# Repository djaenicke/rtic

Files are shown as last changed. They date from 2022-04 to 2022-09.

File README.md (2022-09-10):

<p align="center">
  <h1 align="center">RTIC</h1>
</p>

### The Hardware
The Real Time Interface and Controller (RTIC) is a universal board for low-level robotics control and monitoring. The board can be ordered from [JLCPCB](https://jlcpcb.com/) using the [assembly](pcb/kicad/v2/assembly) and [gerber](pcb/kicad/v2/gerber) files.

#### Key Features
- 4 permanent magnet DC motor outputs
- 4 quadrature encoder inputs
- 6-axis IMU
- NRF24L01 socket for wireless communications
- USB (supports DFU via jumper)
- CAN breakout header

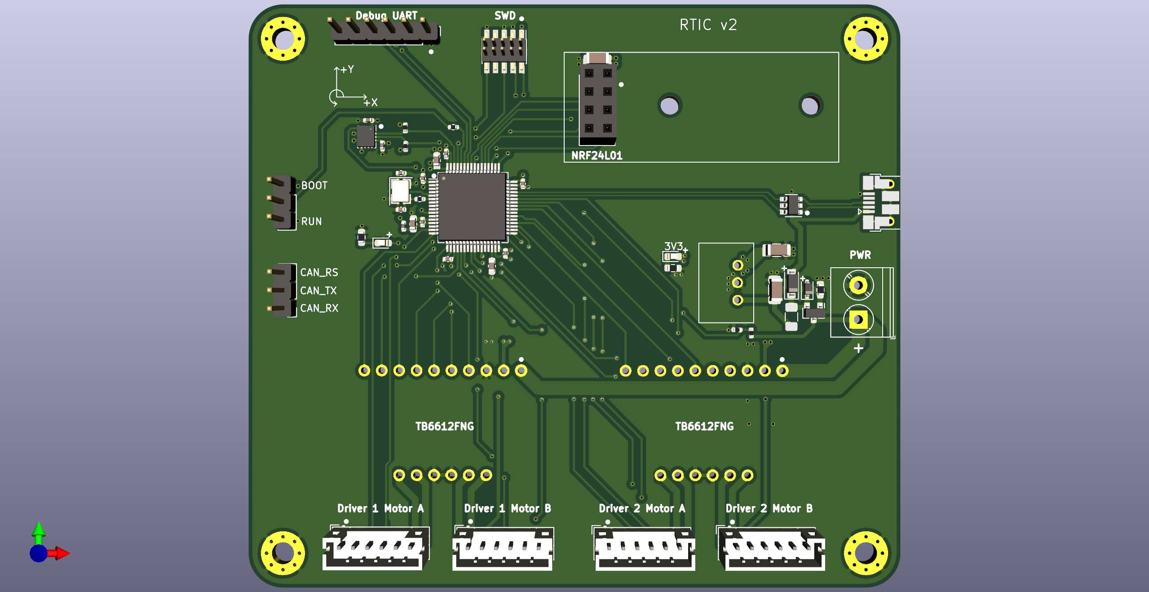
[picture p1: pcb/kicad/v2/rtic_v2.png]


A [compatible 4-wheeled mobile robot base](https://www.amazon.com/Moebius-Mecanum-Platform-Omni-direactional-Raspberry/dp/B083XS2SD7) can be purchased directly from Amazon. :robot:

### Tools Setup ✔️
At a minium you will need the ARM GNU GCC Toolchain, Make and CMake to compile the source and generate executable artifacts.
-   [ARM GNU GCC Toolchain - 10-2020-q4-major](https://developer.arm.com/tools-and-software/open-source-software/developer-tools/gnu-toolchain/gnu-rm/downloads) - Other versions can be used but the current source is actively developed and tested using the 10-2020-q4-major release
-   Make -  Make is shipped with Linux and should already be present on the developers system. If the developer is running Windows they can either use WSL to run a Linux instance or install Make on Windows via [MinGW](https://sourceforge.net/projects/mingw/)
-   [CMake](https://cmake.org/download/)

To flash and debug the target this project uses a couple of different tools. PyOCD, Segger JLink, or STLINK can be used as the programming/debugging medium, and a VScode extension called Cortex-Debug gives a user interface within VScode for stepping through the source, settings breakpoints and viewing registers/variables within the target.
-   [PyOCD](https://github.com/pyocd/pyOCD#installing)
-   [JLink](https://www.segger.com/downloads/jlink/)
-   [STLINK](https://github.com/stlink-org/stlink)
-   [VScode](https://code.visualstudio.com/)
-   [ARM Developer Extension Pack for VScode](https://marketplace.visualstudio.com/items?itemName=Glasslabs.arm-developer-toolkit)

As an alternative to the debuggging tools, dfu-util can be used to program the board using the built in DFU capability of the bootloader.
-   [dfu-util](https://manpages.ubuntu.com/manpages/xenial/man1/dfu-util.1.html)
    - Linux - ```sudo apt-get install dfu-util```

***NOTE: After installing your desired debug toolset, please ensure the chosen application is accessible from the command line (pyocd or JLinkExe)***

To format all source files, you will need to install Clang-Format.
-   [Clang-Format](https://clang.llvm.org/docs/ClangFormat.html)
    - Linux - ```sudo apt-get install clang-format```

### Compiling, Flashing & Testing ✨
After a fresh clone, the ```setup``` scripts can be used to initialize the project. Passing ```release``` as an argument will generate a release build. Otherwise a ```debug``` build is generated.
##### Windows
```console
setup.ps1
```
##### Linux
```console
./setup.sh
```

Once a project has been initialized, the following commands should be ran from the ```build/``` folder

To clean the working directory:
```console
make clean
```

To compile the source:
```console
make -j8
```

To erase the connected target with PyOCD or Segger JLink:
```console
make erase
```

To flash the connected target with PyOCD or Segger JLink:
```console
make flash
```

To flash the connected target via DFU:
```console
make dfu
```

To execute unit tests:
```console
make test
```

To format source files:
```console
make format
```

### Source Documentation Style 📃
Read more about the Source documentation style [here](./doc/DOCUMENTATION_STYLE.md)

### Develop Strategy 📖
Read more about the Git develop strategy used [here](./doc/DEVELOP_STRATEGY.md)

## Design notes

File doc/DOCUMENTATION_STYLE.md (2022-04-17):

### Documentation Style
All of the source files should be commented/documented using Doxygen style comments. This has two benefits: 1.) The code is well documented and more friendly for new developers to come along and understand the code. 2.) VScode can parse these comments and provide hints/tooltips when hovering a mouse over a function, variable or macro name.

#### File Headers
When documenting a File. A ```@file``` keyword is used for the Filename folowed by a ```@brief``` for a quick file description
```c
/*! @file mcp342x.h
 * @brief Public header file for the MCP342x 16-Bit, ADC C driver.
 */
```

#### Variables & Macros
When documenting a variable or macro the comment should be placed on the line before the definition using the ```@brief``` keyword
```c
/*! @brief LSB Value in Volts of a sampled output code */
#define MCP342x_LSB_VAL (0.0000625)
```

#### Typedef Enums, Structs and Unions
When documenting a typedef enum or struct a brief header is placed above the definition to give a description of the Typedef and a single comment is placed on each line of a member.
```c
/*!
 * @brief MCP342x Conversion Modes
 */
typedef enum {
    MCP342x_CM_ONE_SHOT     = 0x00, /* One Shot Conversion */
    MCP342x_CM_CONT         = 0x01, /* Continuous Conversion */
    MCP342x_CM__MAX__       = 0x02, /* Conversion Mode Max */
} mcp342x_conversion_mode_enum;

/*!
 * @brief MCP342x ADC Results
 */
typedef struct
{
    uint16_t outputCode;            /* 16-bit Output Code */
    float voltage;                  /* Sampled Voltage */
} mcp342x_results_t;

/*!
 * @brief MCP342x Configuration Register
 */
typedef union
{
    struct
    {
        uint8_t gain        : 2;    /* Gain */
        uint8_t sample_rate : 2;    /* Sample Rate */
        uint8_t conv_mode   : 1;    /* Conversion Mode */
        uint8_t channel     : 2;    /* Channel */
        uint8_t ready       : 1;    /* Ready Bit */
    } bits;
    uint8_t byte;
} mcp342x_config_t;

```

#### Functions
When documenting a function in your source file (```.c```), you simply need to place a single brief statement. Below is an example of documenting an I2C Read interface
```c
/*!
 * @brief This function pointer API reads I2C data from the specified
 * device on the bus.
 */
int8_t i2c_read(const uint8_t busAddr, uint8_t *data, const uint32_t len) {
    app_return_code_t ret = APP_RET_OK;

    // I2c read function code here

    return ret;
}
```
When documenting the API in your header file (```.h```), the documentation is a bit more involved. Here you will place a brief, as well as defining the parameters and a description of what the return value pertains to. Take note of the ```@param``` variables and their directions (```in/out```). Notice that even though the ```data``` parameter is an input argument, we documented it as an output since we expect the function to manipulate something that the data pointer points to.
```c
/*!
 * @brief This function pointer API reads I2C data from the specified
 * device on the bus.
 *
 * @param[in] busAddr: Address of the device to be read from
 * @param[out] *data: Pointer to the where we should store the read data
 * @param[in] len: Length of data to be read
 *
 * @return The result of reading I2C data
 */
int8_t i2c_read(const uint8_t busAddr, uint8_t *data, const uint32_t len);
```

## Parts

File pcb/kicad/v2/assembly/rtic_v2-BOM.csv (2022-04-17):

Comment | Designator | Footprint | LCSC
10u | C1,C19 | Capacitor_SMD:C_1206_3216Metric | C13585
1u | C11 | Capacitor_SMD:C_0603_1608Metric | C15849
10n | C12 | Capacitor_SMD:C_0402_1005Metric | C15195
2u2 | C13 | Capacitor_SMD:C_0603_1608Metric | C23630
12p | C15,C16 | Capacitor_SMD:C_0402_1005Metric | C1547
22u | C2 | Capacitor_SMD:C_1206_3216Metric | C12891
4u7 | C5 | Capacitor_SMD:C_0603_1608Metric | C19666
100n | C3,C4,C6,C7,C8,C9,C10 | Capacitor_SMD:C_0402_1005Metric | C1525
B5819W | D1 | Diode_SMD:D_SOD-123 | C8598
GREEN | D3 | LED_SMD:LED_0603_1608Metric | C72043
BLUE | D4 | LED_SMD:LED_0603_1608Metric | C72041
12V | D5 | Diode_SMD:D_SOD-323 | C261261
500mA | F1 | Fuse:Fuse_1206_3216Metric | C99561
MountingHole_Pad | H1,H2,H3,H4 | MountingHole:MountingHole_3.2mm_M3_Pad_Via
MountingHole | H5,H6 | MountingHole:MountingHole_2.7mm_M2.5
Screw_Terminal_01x02 | J1 | TerminalBlock_Phoenix:TerminalBlock_Phoenix_PT-1,5-2-5.0-H_1x02_P5.00mm_Horizontal
Conn_01x03 | J10,J11 | Connector_PinHeader_2.54mm:PinHeader_1x03_P2.54mm_Vertical
SWD | J2 | Connector_PinHeader_1.27mm:PinHeader_2x05_P1.27mm_Vertical_SMD
Conn_01x06 | J3 | Connector_PinHeader_2.54mm:PinHeader_1x06_P2.54mm_Vertical
USB_B_Micro | J4 | Connector_USB:USB_Micro-B_Amphenol_10103594-0001LF_Horizontal
D1_MOTORA | J5 | Connector_JST:JST_PH_B6B-PH-K_1x06_P2.00mm_Vertical
D1_MOTORB | J6 | Connector_JST:JST_PH_B6B-PH-K_1x06_P2.00mm_Vertical
D2_MOTORA | J7 | Connector_JST:JST_PH_B6B-PH-K_1x06_P2.00mm_Vertical
D2_MOTORB | J8 | Connector_JST:JST_PH_B6B-PH-K_1x06_P2.00mm_Vertical
Conn_02x04_Odd_Even | J9 | Connector_PinSocket_2.54mm:PinSocket_2x04_P2.54mm_Vertical
39n | L2 | Inductor_SMD:L_0402_1005Metric | C26443
AO3401A | Q1 | Package_TO_SOT_SMD:SOT-23 | C15127
100K | R10 | Resistor_SMD:R_0603_1608Metric | C25803
2.2k | R11,R12 | Resistor_SMD:R_0402_1005Metric | C25879
3.3k | R13 | Resistor_SMD:R_0402_1005Metric | C25890
1k | R14 | Resistor_SMD:R_0402_1005Metric | C11702
10k | R7 | Resistor_SMD:R_0402_1005Metric | C25744
47 | R8 | Resistor_SMD:R_0402_1005Metric | C25118
1k5 | R6,R9 | Resistor_SMD:R_0603_1608Metric | C22843
VR10S3V3 | U1 | dj:VR10S3V3
STM32F412RETx | U2 | Package_QFP:LQFP-64_10x10mm_P0.5mm | C89374
USBLC6-2SC6 | U3 | Package_TO_SOT_SMD:SOT-23-6 | C7519
BMI160 | U4 | Package_LGA:Bosch_LGA-14_3x2.5mm_P0.5mm | C94021
TB6612FNG_BB | U5,U6 | dj:TB6612FNG_BB
16MHz | Y1 | Crystal:Crystal_SMD_3225-4Pin_3.2x2.5mm | C13738

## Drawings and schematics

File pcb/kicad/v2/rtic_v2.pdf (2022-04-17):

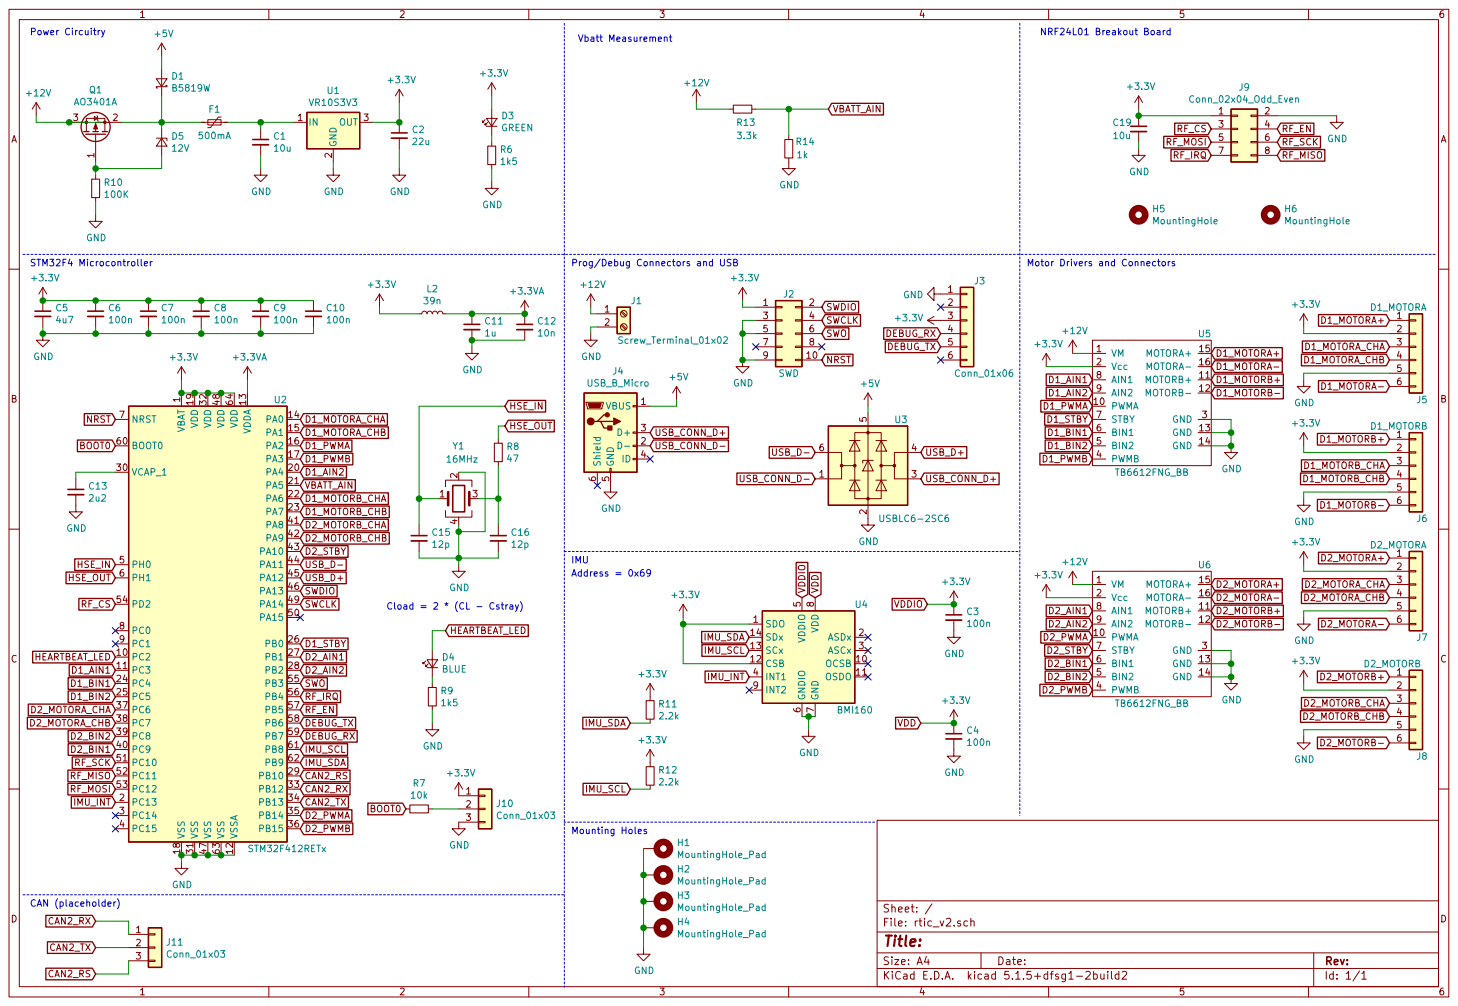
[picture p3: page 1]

Vbatt Measurement Power Circuitry

Prog/Debug Connectors and USB

Motor Drivers and Connectors Address = 0x69

1 VCAP_1 30 VDD 19 VDD 32 VDD 48 VDD 64 VDDA 13 VSS 18 VSS 31 VSS 47 VSS 63 VSSA 12 U2 STM32F412RETx GND

File: rtic_v2.sch Sheet: / GND

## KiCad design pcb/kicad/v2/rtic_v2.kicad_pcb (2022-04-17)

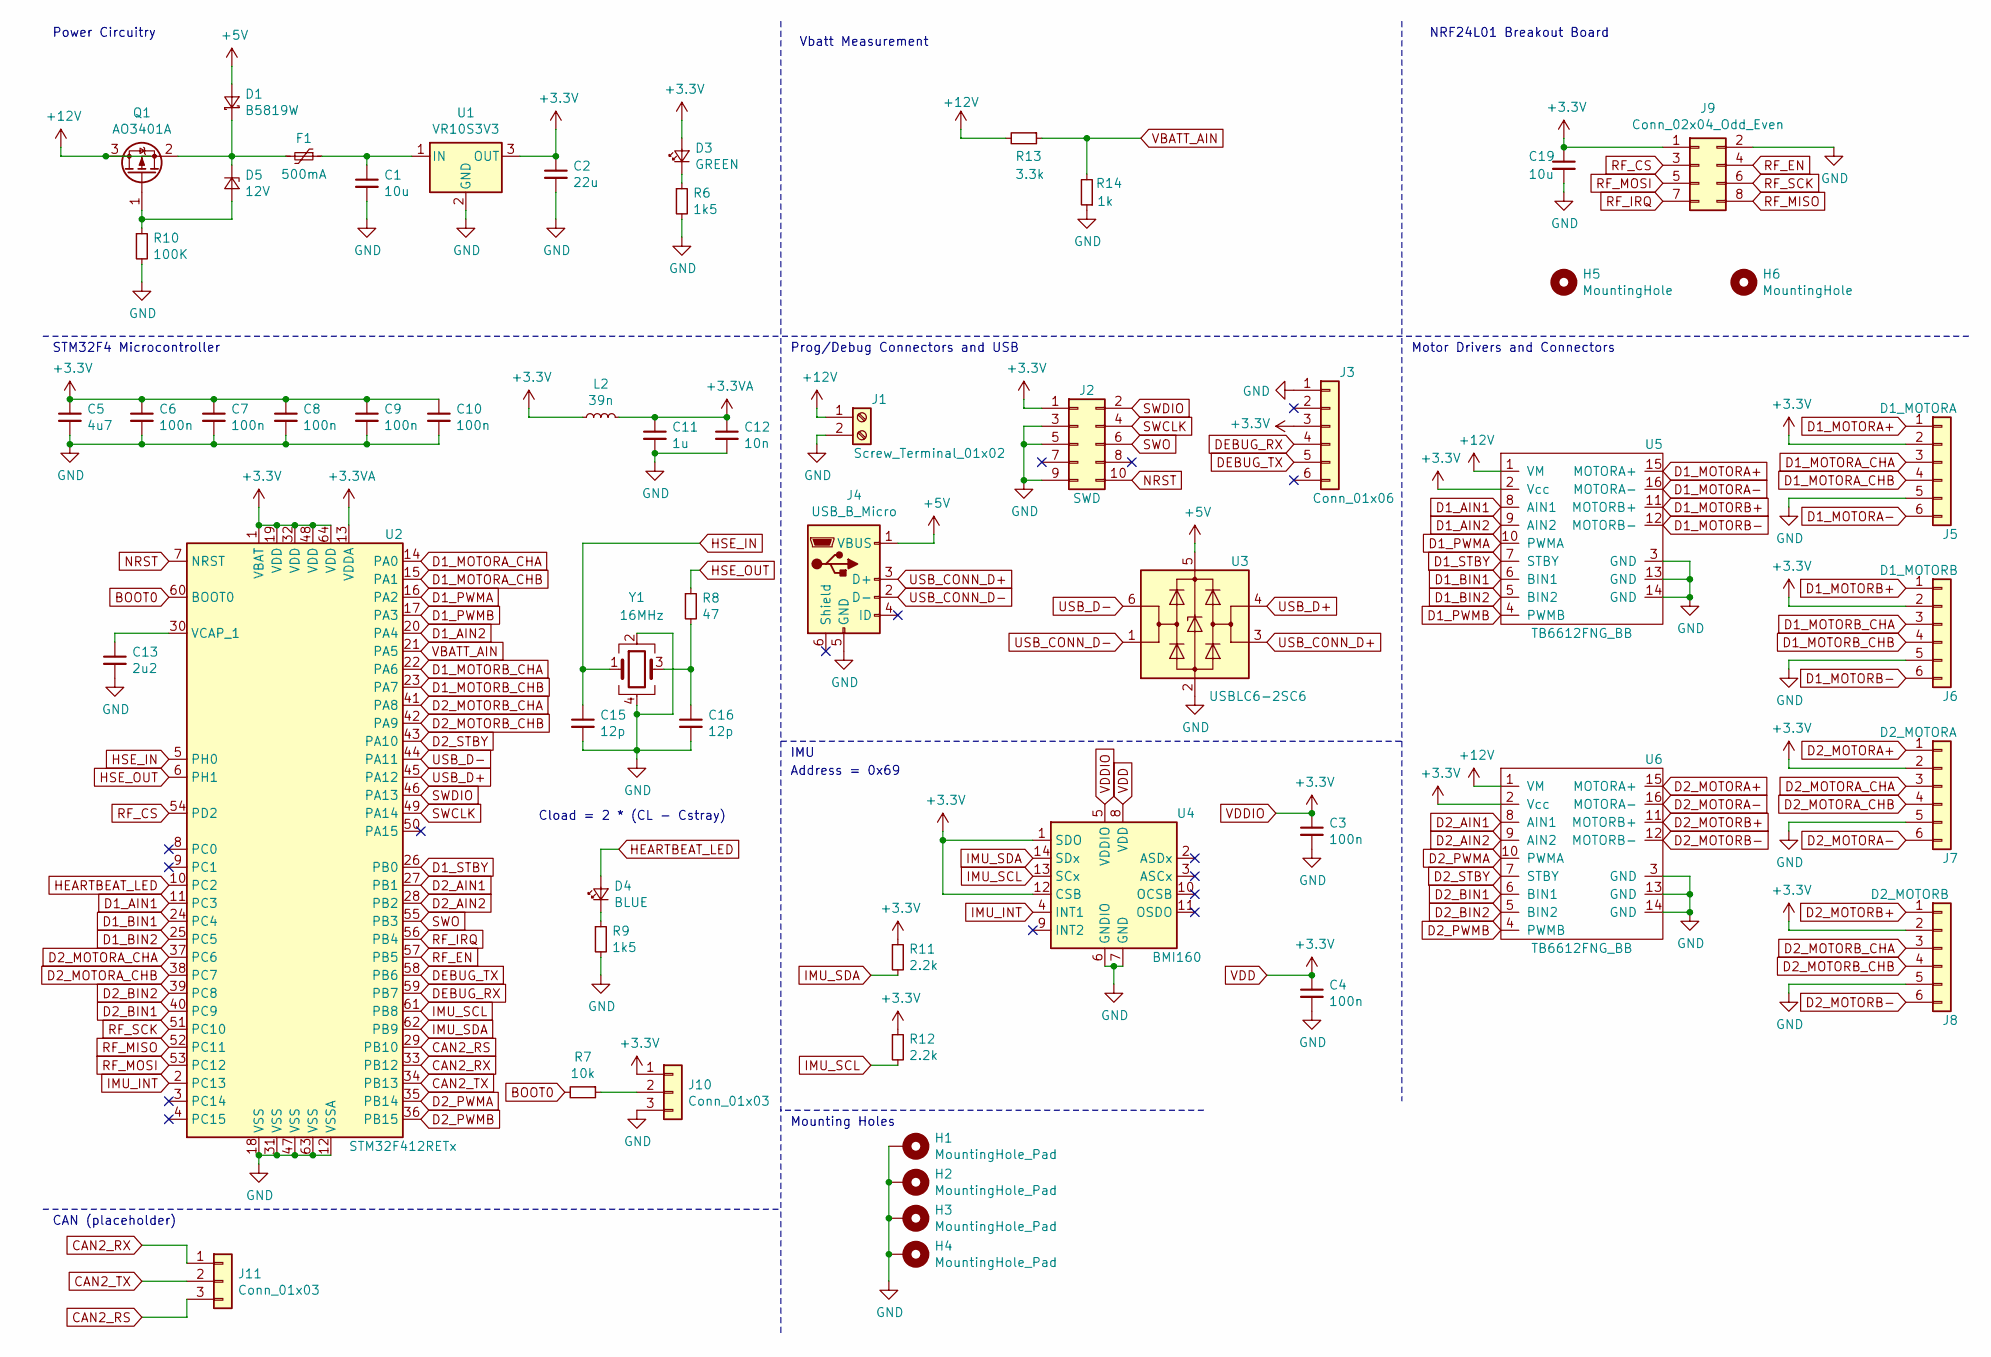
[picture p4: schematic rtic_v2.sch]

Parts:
C1, C19: 10u; C_1206_3216Metric; LCSC Part # C13585
C2: 22u; C_1206_3216Metric; LCSC Part # C12891
C3, C4, C6, C7, C8, C9, C10: 100n; C_0402_1005Metric; LCSC Part # C1525
C5: 4u7; C_0603_1608Metric; LCSC Part # C19666
C11: 1u; C_0603_1608Metric; LCSC Part # C15849
C12: 10n; C_0402_1005Metric; LCSC Part # C15195
C13: 2u2; C_0603_1608Metric; LCSC Part # C23630
C15, C16: 12p; C_0402_1005Metric; LCSC Part # C1547
D1: B5819W; D_SOD-123; LCSC Part # C8598
D3: GREEN; LED_0603_1608Metric; LCSC Part # C72043
D4: BLUE; LED_0603_1608Metric; LCSC Part # C72041
D5: 12V; D_SOD-323; LCSC Part # C261261
F1: 500mA; Fuse_1206_3216Metric; LCSC Part # C99561
H1, H2, H3, H4: MountingHole_Pad; MountingHole_3.2mm_M3_Pad_Via
H5, H6: MountingHole; MountingHole_2.7mm_M2.5
J1: Screw_Terminal_01x02; TerminalBlock_Phoenix_PT-1,5-2-5.0-H_1x02_P5.00mm_Horizontal
J2: SWD; PinHeader_2x05_P1.27mm_Vertical_SMD
J3: Conn_01x06; PinHeader_1x06_P2.54mm_Vertical
J4: USB_B_Micro; USB_Micro-B_Amphenol_10103594-0001LF_Horizontal
J5: D1_MOTORA; JST_PH_B6B-PH-K_1x06_P2.00mm_Vertical
J6: D1_MOTORB; JST_PH_B6B-PH-K_1x06_P2.00mm_Vertical
J7: D2_MOTORA; JST_PH_B6B-PH-K_1x06_P2.00mm_Vertical
J8: D2_MOTORB; JST_PH_B6B-PH-K_1x06_P2.00mm_Vertical
J9: Conn_02x04_Odd_Even; PinSocket_2x04_P2.54mm_Vertical
J10, J11: Conn_01x03; PinHeader_1x03_P2.54mm_Vertical
L2: 39n; L_0402_1005Metric; LCSC Part # C26443
Q1: AO3401A; SOT-23; LCSC Part # C15127
R6, R9: 1k5; R_0603_1608Metric; LCSC Part # C22843
R7: 10k; R_0402_1005Metric; LCSC Part # C25744
R8: 47; R_0402_1005Metric; LCSC Part # C25118
R10: 100K; R_0603_1608Metric; LCSC Part # C25803
R11, R12: 2.2k; R_0402_1005Metric; LCSC Part # C25879
R13: 3.3k; R_0402_1005Metric; LCSC Part # C25890
R14: 1k; R_0402_1005Metric; LCSC Part # C11702
U1: VR10S3V3
U2: STM32F412RETx; LQFP-64_10x10mm_P0.5mm; LCSC Part # C89374
U3: USBLC6-2SC6; SOT-23-6; LCSC Part # C7519
U4: BMI160; Bosch_LGA-14_3x2.5mm_P0.5mm; LCSC Part # C94021
U5, U6: TB6612FNG_BB
Y1: 16MHz; Crystal_SMD_3225-4Pin_3.2x2.5mm; LCSC Part # C13738

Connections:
+3.3VA: C11.1, C12.1, L2.2, U2.13 (VDDA)
+5V: D1.2 (A), J4.1 (VBUS), U3.5 (VBUS)
+12V: J1.1, Q1.3 (D), R13.2, U5.1 (VM), U6.1 (VM)
BOOT0: R7.2, U2.60 (BOOT0)
CAN2_RS: J11.3, U2.29 (PB10)
CAN2_RX: J11.1, U2.33 (PB12)
CAN2_TX: J11.2, U2.34 (PB13)
D1_AIN1: U2.11 (PC3), U5.8 (AIN1)
D1_AIN2: U2.20 (PA4), U5.9 (AIN2)
D1_BIN1: U2.24 (PC4), U5.6 (BIN1)
D1_BIN2: U2.25 (PC5), U5.5 (BIN2)
D1_MOTORA+: J5.1, U5.15 (MOTORA+)
D1_MOTORA-: J5.6, U5.16 (MOTORA-)
D1_MOTORA_CHA: J5.3, U2.14 (PA0)
D1_MOTORA_CHB: J5.4, U2.15 (PA1)
D1_MOTORB+: J6.1, U5.11 (MOTORB+)
D1_MOTORB-: J6.6, U5.12 (MOTORB-)
D1_MOTORB_CHA: J6.3, U2.22 (PA6)
D1_MOTORB_CHB: J6.4, U2.23 (PA7)
D1_PWMA: U2.16 (PA2), U5.10 (PWMA)
D1_PWMB: U2.17 (PA3), U5.4 (PWMB)
D1_STBY: U2.26 (PB0), U5.7 (STBY)
D2_AIN1: U2.27 (PB1), U6.8 (AIN1)
D2_AIN2: U2.28 (PB2), U6.9 (AIN2)
D2_BIN1: U2.40 (PC9), U6.6 (BIN1)
D2_BIN2: U2.39 (PC8), U6.5 (BIN2)
D2_MOTORA+: J7.1, U6.15 (MOTORA+)
D2_MOTORA-: J7.6, U6.16 (MOTORA-)
D2_MOTORA_CHA: J7.3, U2.37 (PC6)
D2_MOTORA_CHB: J7.4, U2.38 (PC7)
D2_MOTORB+: J8.1, U6.11 (MOTORB+)
D2_MOTORB-: J8.6, U6.12 (MOTORB-)
D2_MOTORB_CHA: J8.3, U2.41 (PA8)
D2_MOTORB_CHB: J8.4, U2.42 (PA9)
D2_PWMA: U2.35 (PB14), U6.10 (PWMA)
D2_PWMB: U2.36 (PB15), U6.4 (PWMB)
D2_STBY: U2.43 (PA10), U6.7 (STBY)
DEBUG_RX: J3.4, U2.59 (PB7)
DEBUG_TX: J3.5, U2.58 (PB6)
GND: C1.2, C2.2, C3.2, C4.2, C5.2, C6.2, C7.2, C8.2, C9.2, C10.2, C11.2, C12.2, C13.2, C15.2, C16.2, C19.2, H1.1, H2.1, H3.1, H4.1, J1.2, J2.3, J2.5, J2.9, J3.1, J4.5 (GND), J5.5, J6.5, J7.5, J8.5, J9.2, J10.3, R6.2, R9.2, R10.2, R14.1, U1.2 (GND), U2.12 (VSSA), U2.18 (VSS), U2.31 (VSS), U2.47 (VSS), U2.63 (VSS), U3.2 (GND), U4.6 (GNDIO), U4.7 (GND), U5.3 (GND), U5.13 (GND), U5.14 (GND), U6.3 (GND), U6.13 (GND), U6.14 (GND), Y1.2, Y1.4
HEARTBEAT_LED: D4.2 (A), U2.10 (PC2)
HSE_IN: C15.1, U2.5 (PH0), Y1.1
HSE_OUT: R8.1, U2.6 (PH1)
IMU_INT: U2.2 (PC13), U4.4 (INT1)
IMU_SCL: R12.2, U2.61 (PB8), U4.13 (SCx)
IMU_SDA: R11.2, U2.62 (PB9), U4.14 (SDx)
NRST: J2.10, U2.7 (NRST)
unnamed: C1.1, F1.1, U1.1 (IN)
unnamed: C13.1, U2.30 (VCAP_1)
unnamed: C16.1, R8.2, Y1.3
unnamed: D1.1 (K), D5.1 (K), F1.2, Q1.2 (S)
unnamed: D3.1 (K), R6.1
unnamed: D4.1 (K), R9.1
unnamed: D5.2 (A), Q1.1 (G), R10.1
unnamed: J10.2, R7.1
RF_CS: J9.3, U2.54 (PD2)
RF_EN: J9.4, U2.57 (PB5)
RF_IRQ: J9.7, U2.56 (PB4)
RF_MISO: J9.8, U2.52 (PC11)
RF_MOSI: J9.5, U2.53 (PC12)
RF_SCK: J9.6, U2.51 (PC10)
SWCLK: J2.4, U2.49 (PA14)
SWDIO: J2.2, U2.46 (PA13)
SWO: J2.6, U2.55 (PB3)
USB_CONN_D+: J4.3 (D+), U3.3 (I/O2)
USB_CONN_D-: J4.2 (D-), U3.1 (I/O1)
USB_D+: U2.45 (PA12), U3.4 (I/O2)
USB_D-: U2.44 (PA11), U3.6 (I/O1)
VBATT_AIN: R13.1, R14.2, U2.21 (PA5)
VDD: C2.1, C3.1, C4.1, C5.1, C6.1, C7.1, C8.1, C9.1, C10.1, C19.1, D3.2 (A), J2.1, J3.3, J5.2, J6.2, J7.2, J8.2, J9.1, J10.1, L2.1, R11.1, R12.1, U1.3 (OUT), U2.1 (VBAT), U2.19 (VDD), U2.32 (VDD), U2.48 (VDD), U2.64 (VDD), U4.1 (SDO), U4.5 (VDDIO), U4.8 (VDD), U4.12 (CSB), U5.2 (Vcc), U6.2 (Vcc)

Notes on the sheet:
Cload = 2 * (CL - Cstray)
STM32F4 Microcontroller
Power Circuitry
Prog/Debug Connectors and USB
IMU
Mounting Holes
Motor Drivers and Connectors
NRF24L01 Breakout Board
CAN (placeholder)
Vbatt Measurement
Address = 0x69

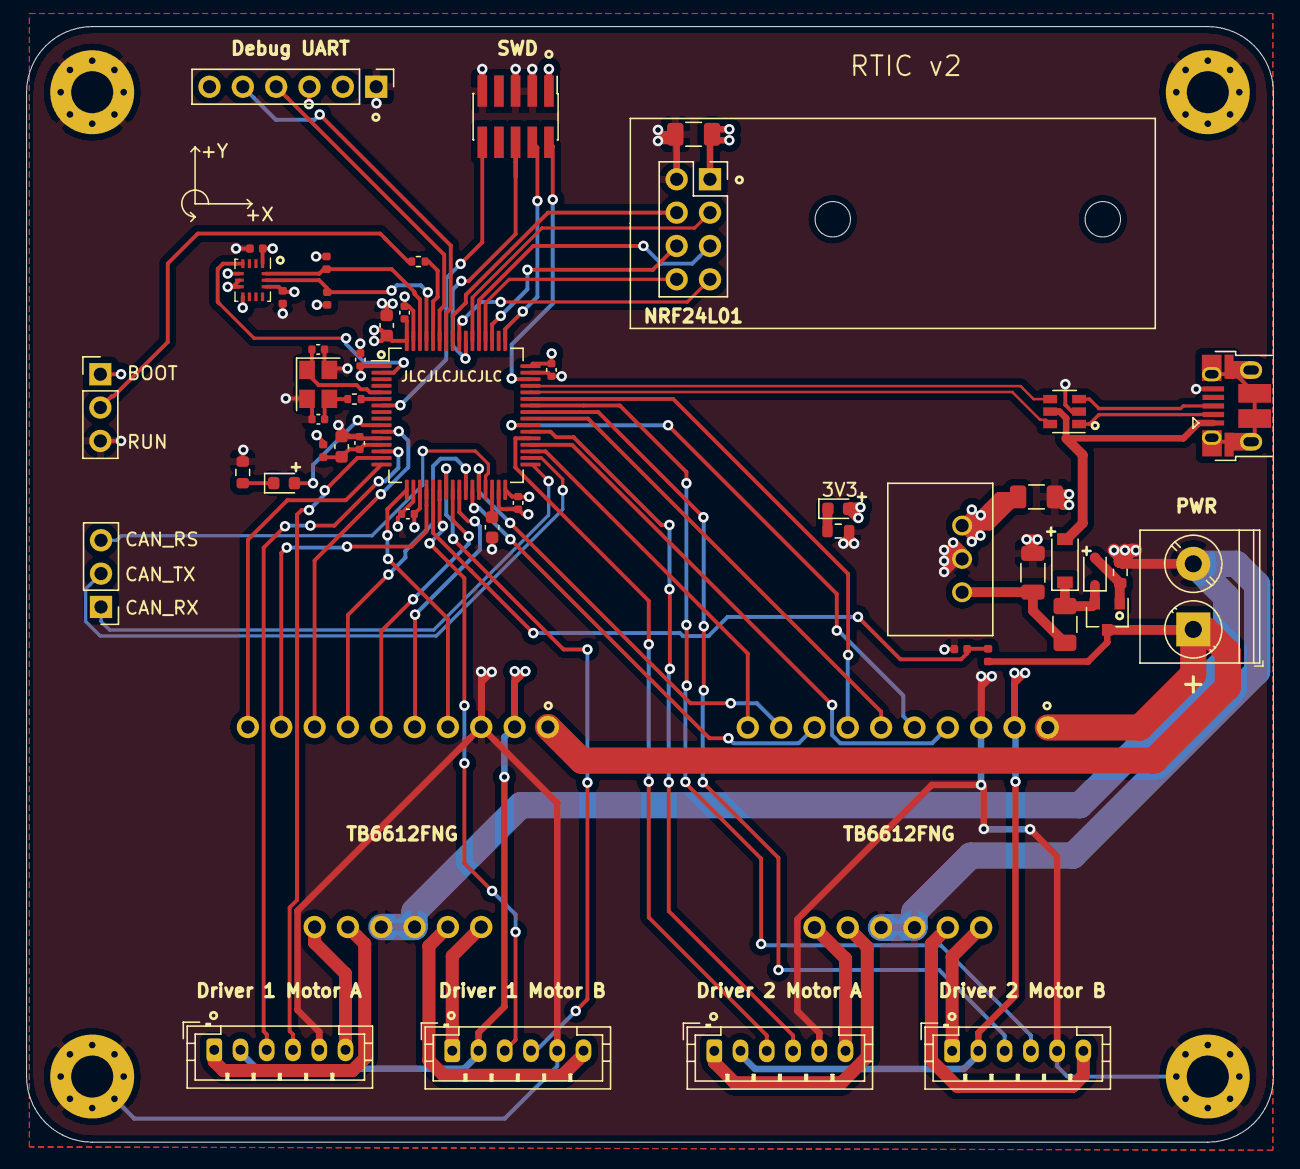
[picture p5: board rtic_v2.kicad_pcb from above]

Board: 4 copper layers, 95.0 x 85.0 mm, 56 parts (0 on the bottom side), 70 nets.

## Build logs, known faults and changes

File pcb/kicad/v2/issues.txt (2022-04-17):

Issues:

   - 12V connector is reversed
   - Overvoltage protection does not work
   - D5 is undersized
   - VR10S3V3 requires a minimum of 6V at input, so USB alone will not power the board
   - silkscreen rectangle for NRF24L01 is placed properly

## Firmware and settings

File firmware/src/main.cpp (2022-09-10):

#include <stdio.h>

#include "board.h"
#include "cmsis_os.h"
#include "digital_out.h"
#include "imu_interface.h"
#include "io.h"
#include "motor_controls.h"
#include "rf_interface.h"
#include "serial_logger.h"
#include "threads.h"

static void threadHeartbeat(const void* argument);

// clang-format off
static osThreadId heartbeat_thread_handle;
static char heartbeat_thread_name[] = "HeartbeatThread";
const osThreadDef_t heartbeat_thread_def = { 
  heartbeat_thread_name,
  threadHeartbeat,
  HEARTBEAT_PRIORITY,
  0u,
  HEARTBEAT_STACK_SIZE_WORDS,
  NULL,
  NULL
};

static osThreadId serial_logger_thread_handle;
static char serial_logger_thread_name[] = "SerialLoggerThread";
const osThreadDef_t serial_logger_thread_def = { 
  serial_logger_thread_name,
  threadSerialLogger,
  SERIAL_LOGGER_PRIORITY,
  0u,
  SERIAL_LOGGER_STACK_SIZE_WORDS,
  NULL,
  NULL
};

static osThreadId rf_interface_thread_handle;
static char rf_interface_thread_name[] = "RfInterfaceThread";
const osThreadDef_t rf_interface_thread_def = { 
  rf_interface_thread_name,
  threadRfInterface,
  RF_INTERFACE_PRIORITY,
  0u,
  RF_INTERFACE_STACK_SIZE_WORDS,
  NULL,
  NULL
};

static osThreadId imu_interface_thread_handle;
static char imu_interface_thread_name[] = "ImuInterfaceThread";
const osThreadDef_t imu_interface_thread_def = { 
  imu_interface_thread_name,
  threadImuInterface,
  IMU_INTERFACE_PRIORITY,
  0u,
  IMU_INTERFACE_STACK_SIZE_WORDS,
  NULL,
  NULL
};

static osThreadId motor_controls_thread_handle;
static char motor_controls_thread_name[] = "MotorControlsThread";
const osThreadDef_t motor_controls_thread_def = { 
  motor_controls_thread_name,
  threadMotorControls,
  MOTOR_CONTROLS_PRIORITY,
  0u,
  MOTOR_CONTROLS_STACK_SIZE_WORDS,
  NULL,
  NULL
};
// clang-format on

int main(void)
{
  // Configure the system prior to starting the threads
  initSerialLogger(LOG_DEBUG);
  initUiMessageBuffer();

  // Create the threads
  heartbeat_thread_handle = osThreadCreate(&heartbeat_thread_def, NULL);
  serial_logger_thread_handle = osThreadCreate(&serial_logger_thread_def, NULL);
  rf_interface_thread_handle = osThreadCreate(&rf_interface_thread_def, NULL);
  imu_interface_thread_handle = osThreadCreate(&imu_interface_thread_def, NULL);
  motor_controls_thread_handle = osThreadCreate(&motor_controls_thread_def, NULL);

  // Start the scheduler
  osKernelStart();

  return 0;
}

static void threadHeartbeat(const void* argument)
{
  static hal::DigitalOut heartbeat(HEARTBEAT_LED);
  static TickType_t last_wake_time = xTaskGetTickCount();
  const TickType_t cycle_time_ticks = HEARTBEAT_PERIOD_MS * portTICK_PERIOD_MS;

  logMessage(LOG_DEBUG, "HeartbeatThread started.\r\n");

  for (;;)
  {
    vTaskDelayUntil(&last_wake_time, cycle_time_ticks);
    heartbeat.toggle();
  }
}

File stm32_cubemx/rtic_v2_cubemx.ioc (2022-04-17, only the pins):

Mcu.UserName=STM32F412RETx
PA0.GPIO_Label=D1_MOTORA_CHA
PA0.Signal=S_TIM5_CH1
PA1.GPIO_Label=D1_MOTORA_CHB
PA1.Signal=S_TIM5_CH2
PA10.GPIO_Label=D2_STBY
PA10.Signal=GPIO_Output
PA11.Signal=USB_OTG_FS_DM
PA12.Signal=USB_OTG_FS_DP
PA13.Signal=SYS_JTMS-SWDIO
PA14.Signal=SYS_JTCK-SWCLK
PA2.GPIO_Label=D1_PWMA
PA2.Signal=S_TIM9_CH1
PA3.GPIO_Label=D1_PWMB
PA3.Signal=S_TIM9_CH2
PA4.GPIO_Label=D1_AIN2
PA4.Signal=GPIO_Output
PA5.GPIO_Label=VBATT_AIN
PA5.Signal=ADCx_IN5
PA6.GPIO_Label=D1_MOTORB_CHA
PA6.Signal=S_TIM3_CH1
PA7.GPIO_Label=D1_MOTORB_CHB
PA7.Signal=S_TIM3_CH2
PA8.GPIO_Label=D2_MOTORB_CHA
PA8.Signal=GPXTI8
PA9.GPIO_Label=D2_MOTORB_CHB
PA9.Signal=GPXTI9
PB0.GPIO_Label=D1_STBY
PB0.Signal=GPIO_Output
PB1.GPIO_Label=D2_AIN1
PB1.Signal=GPIO_Output
PB10.GPIO_Label=CAN2_RS
PB10.Signal=GPIO_Output
PB12.Signal=CAN2_RX
PB13.Signal=CAN2_TX
PB14.GPIO_Label=D2_PWMA
PB14.Signal=S_TIM12_CH1
PB15.GPIO_Label=D2_PWMB
PB15.Signal=S_TIM12_CH2
PB2.GPIO_Label=D2_AIN2
PB2.Signal=GPIO_Output
PB3.Signal=SYS_JTDO-SWO
PB4.GPIO_Label=RF_IRQ
PB4.Signal=GPIO_Input
PB5.GPIO_Label=RF_EN
PB5.Signal=GPIO_Output
PB6.GPIO_Label=DEBUG_TX
PB6.Signal=USART1_TX
PB7.GPIO_Label=DEBUG_RX
PB7.Signal=USART1_RX
PB8.GPIO_Label=IMU_SCL
PB8.Signal=I2C1_SCL
PB9.GPIO_Label=IMU_SDA
PB9.Signal=I2C1_SDA
PC10.GPIO_Label=RF_SCK
PC10.Signal=SPI3_SCK
PC11.GPIO_Label=RF_MISO
PC11.Signal=SPI3_MISO
PC12.GPIO_Label=RF_MOSI
PC12.Signal=SPI3_MOSI
PC13.GPIO_Label=IMU_INT
PC13.Signal=GPIO_Input
PC14-OSC32_IN.Signal=RCC_OSC32_IN
PC15-OSC32_OUT.Signal=RCC_OSC32_OUT
PC2.GPIO_Label=HEARTBEAT_LED
PC2.Signal=GPIO_Output
PC3.GPIO_Label=D1_AIN1
PC3.Signal=GPIO_Output
PC4.GPIO_Label=D1_BIN1
PC4.Signal=GPIO_Output
PC5.GPIO_Label=D1_BIN2
PC5.Signal=GPIO_Output
PC6.GPIO_Label=D2_MOTORA_CHA
PC6.Signal=GPXTI6
PC7.GPIO_Label=D2_MOTORA_CHB
PC7.Signal=GPXTI7
PC8.GPIO_Label=D2_BIN2
PC8.Signal=GPIO_Output
PC9.GPIO_Label=D2_BIN1
PC9.Signal=GPIO_Output
PD2.GPIO_Label=RF_CS
PD2.Signal=GPIO_Output

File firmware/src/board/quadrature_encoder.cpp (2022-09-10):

#include "quadrature_encoder.h"

#include <cassert>

namespace hal
{
static const uint8_t NUM_INTERRUPT_INPUTS = 5u;
static const uint8_t MIN_SUPPORTED_INTERRUPT_PIN_NUM = 5u;
static const uint8_t MAX_SUPPORTED_INTERRUPT_PIN_NUM = 9u;
static const int8_t LOOKUP_TABLE[] = { 0, -1, 1, 0, 1, 0, 0, -1, -1, 0, 0, 1, 0, 1, -1, 0 };

static hal::QuadratureEncoder* interrupt_encoders[NUM_INTERRUPT_INPUTS];

QuadratureEncoder::QuadratureEncoder(const Pin& cha, const Pin& chb, const EncoderPolarity polarity)
    : HwTimer(255, TimerMode::ENCODER_4X_MODE, 0.0f),
      _polarity(polarity),
      _timer_mode(false),
      _encoder_pulses(0),
      _encoder_value(0),
      _cha(cha, GpioMode::INPUT_BOTH_INT, hal::GpioPullType::NO_PULL, 0U, GpioSpeed::VERY_HIGH),
      _chb(chb, GpioMode::INPUT_BOTH_INT, hal::GpioPullType::NO_PULL, 0U, GpioSpeed::VERY_HIGH)
{
  if ((cha.port == chb.port) && (cha.num == chb.num))
  {
    assert(0);
  }

  if ((cha.num >= MIN_SUPPORTED_INTERRUPT_PIN_NUM) && (cha.num <= MAX_SUPPORTED_INTERRUPT_PIN_NUM))
  {
    interrupt_encoders[cha.num - MIN_SUPPORTED_INTERRUPT_PIN_NUM] = this;
  }
  else
  {
    assert(0);
  }

  if ((chb.num >= MIN_SUPPORTED_INTERRUPT_PIN_NUM) && (chb.num <= MAX_SUPPORTED_INTERRUPT_PIN_NUM))
  {
    interrupt_encoders[chb.num - MIN_SUPPORTED_INTERRUPT_PIN_NUM] = this;
  }
  else
  {
    assert(0);
  }
}

QuadratureEncoder::QuadratureEncoder(const uint8_t timer_instance, const GPIO& cha, const GPIO& chb,
                                     const EncoderPolarity polarity)
    : HwTimer(timer_instance, TimerMode::ENCODER_4X_MODE, 0.0f),
      _polarity(polarity),
      _timer_mode(true),
      _encoder_pulses(0),
      _encoder_value(0),
      _cha(cha),
      _chb(chb)
{
}

void QuadratureEncoder::start(void)
{
  if (_timer_mode)
  {
    HAL_TIM_Encoder_Start(&_timer_handle, TIM_CHANNEL_ALL);
  }
  else
  {
    HAL_NVIC_SetPriority(EXTI9_5_IRQn, 14, 0);
    HAL_NVIC_EnableIRQ(EXTI9_5_IRQn);
  }
}

void QuadratureEncoder::stop(void)
{
  if (_timer_mode)
  {
    HAL_TIM_Encoder_Stop(&_timer_handle, TIM_CHANNEL_ALL);
  }
  else
  {
    HAL_NVIC_DisableIRQ(EXTI9_5_IRQn);
  }
}

int32_t QuadratureEncoder::getPulses(void)
{
  int32_t temp = 0;

  if (_timer_mode)
  {
    temp = _timer_handle.Instance->CNT;
    _timer_handle.Instance->CNT = 0;
    // apply polarity based on which direction the counter is counting
    if (temp > _max_pulses_per_cycle)
    {
      temp -= UINT16_MAX;
    }
  }
  else  // interrupt mode
  {
    stop();
    temp = _encoder_pulses;
    _encoder_pulses = 0;
    start();
  }

  return (temp * static_cast<int32_t>(_polarity));
}

void QuadratureEncoder::setMaxPulsesPerCycle(const uint16_t max_pulses)
{
  _max_pulses_per_cycle = max_pulses;
}

void QuadratureEncoder::_pinChangeISR(void)
{
  _encoder_value = _encoder_value << 2;
  _encoder_value = _encoder_value | (_cha << 1) | _chb;
  _encoder_pulses += LOOKUP_TABLE[_encoder_value & 0b1111];
}

}  // namespace hal

extern "C"
{
  void EXTI9_5_IRQHandler(void)
  {
    if (__HAL_GPIO_EXTI_GET_IT(GPIO_PIN_5) != RESET)
    {
      if (NULL != hal::interrupt_encoders[0])
      {
        hal::interrupt_encoders[0]->_pinChangeISR();
      }
      __HAL_GPIO_EXTI_CLEAR_IT(GPIO_PIN_5);
    }

    if (__HAL_GPIO_EXTI_GET_IT(GPIO_PIN_6) != RESET)
    {
      if (NULL != hal::interrupt_encoders[1])
      {
        hal::interrupt_encoders[1]->_pinChangeISR();
      }
      __HAL_GPIO_EXTI_CLEAR_IT(GPIO_PIN_6);
    }

    if (__HAL_GPIO_EXTI_GET_IT(GPIO_PIN_7) != RESET)
    {
      if (NULL != hal::interrupt_encoders[2])
      {
        hal::interrupt_encoders[2]->_pinChangeISR();
      }
      __HAL_GPIO_EXTI_CLEAR_IT(GPIO_PIN_7);
    }

    if (__HAL_GPIO_EXTI_GET_IT(GPIO_PIN_8) != RESET)
    {
      if (NULL != hal::interrupt_encoders[3])
      {
        hal::interrupt_encoders[3]->_pinChangeISR();
      }
      __HAL_GPIO_EXTI_CLEAR_IT(GPIO_PIN_8);
    }

    if (__HAL_GPIO_EXTI_GET_IT(GPIO_PIN_9) != RESET)
    {
      if (NULL != hal::interrupt_encoders[4])
      {
        hal::interrupt_encoders[4]->_pinChangeISR();
      }
      __HAL_GPIO_EXTI_CLEAR_IT(GPIO_PIN_9);
    }
  }
}

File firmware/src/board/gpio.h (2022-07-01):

#ifndef GPIO_H
#define GPIO_H (1)

#include <cstdint>

#include "stm32f4xx_hal.h"

namespace hal
{
const uint8_t NO_GPIO_ALT_FUNCTION = 0;

enum class Port
{
  A = 0,
  B,
  C,
  D,
  H,

  NUM_PORTS
};

enum class GpioMode
{
  INPUT = 0,
  OUTPUT_PUSH_PULL,
  OUTPUT_OPEN_DRAIN,
  AF_PUSH_PULL,
  AF_OPEN_DRAIN,
  ANALOG,
  INPUT_RISING_INT,
  INPUT_FALLING_INT,
  INPUT_BOTH_INT,

  NUM_MODES
};

enum class GpioSpeed
{
  LOW = 0,
  MEDIUM,
  HIGH,
  VERY_HIGH
};

struct Pin
{
  Port port;
  uint8_t num;
  Pin(const Port port, const uint8_t num) : port(port), num(num) {};
};

enum class GpioPullType
{
  NO_PULL = 0,
  PULL_UP,
  PULL_DOWN,

  NUM_PULL_TYPES
};

class GPIO
{
 public:
  GPIO(const Pin& pin, const GpioMode mode, const GpioPullType pull = GpioPullType::NO_PULL,
       const uint8_t alt_function = NO_GPIO_ALT_FUNCTION, const GpioSpeed speed = GpioSpeed::LOW);
  operator uint8_t();

 protected:
  GPIO_TypeDef* _port_ptr;
  uint16_t _pin_select;
};

}  // namespace hal

#endif  // GPIO_H (1)

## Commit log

2022-04-02 added STM32F4xx HAL and set project specific CMake variables
2022-04-03 initial implementation of board.c
2022-04-03 added kicad, assembly, and gerber files
    [rtic_v2-BOM.csv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]
2022-04-03 added cubemx ioc for v2 pcb
2022-04-17 updated heartbeat LED to use DigitalOut class
2022-04-17 added HwTimer class to enable PWM and quadrature encoders functionality
2022-04-17 added PWM class
2022-04-17 added TB6612 class and tested on all 4 motors
2022-04-17 added QuadratureEncoder class and fixed UART
    [io.h, main.cpp, quadrature_encoder.cpp]
2022-04-17 updated rear encoders to use interrupts in stm32 cubemx configuration
2022-04-21 split TB6612 class into MotorDriver to separate the two outputs
2022-04-23 created initial threads
2022-07-01 added VoltageMonitor class
2022-07-01 motor controllers working in open loop
2022-07-03 added I2C driver and verified the BMI160 interface
2022-07-03 added BMI160 driver
2022-07-03 added proper callbacks to IMU class
2022-07-03 added nrf24 driver
2022-07-03 updated method names to camel case
